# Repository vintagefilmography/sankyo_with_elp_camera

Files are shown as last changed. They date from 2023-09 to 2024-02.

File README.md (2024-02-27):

# sankyo_with_elp_camera  

elp_12mm_lens

This project is based on a Sankyo projector and ELP camera.  
Parts:  
Sankyo1000 projector  
The camera used is the usb ELP model ELP-USBFHD04H-FV. It uses an AR0330 sensor with 1080P resolution. 
Camera:  
https://www.amazon.com/gp/product/B01E8OX212/  
Light  
https://www.amazon.com/ULANZI-Waterproof-Lighting-Dimmable-Photography/dp/B098W63FJ5/  
Here is the result:  
[https://drive.google.com/file/d/1i-V...usp=share_link](https://drive.google.com/file/d/1_k86P1xBqTre0maZQDL-aEWelFFEkU7V/view?usp=sharing)  

This was scanned with the projector speed set to minimum which turns out to be around 7 frames per second.  

## Projector Mods
The 3 blade shutter wheel has to be removed. This is a bit involved project.
Refer to the following page for insstructions.  
https://github.com/vintagefilmography/Sankyo_shutter_wheel_removal  
https://github.com/vintagefilmography/Sankyo_gatemask_removal_v1  
Read both instructions and replace the gate mask once the shutter assembly is out.  
The heat shield and the fan shroud also have to be removed to provide enough space for the trigger components.  
Do not throw out any of the screws, you will need them later.
Replace the lamap with the LED light. You will have to 3D print the lamp bracket from the mechanical folder here.
It consists of two parts. Use 3mm screws. 
  

Print the camera adapter and attach it to the camera using 2mm screws and nuts.
Remove the old lens by pulling out on the focus knob (spring loaded) and by sliding the lensout. 
Slide the ecamera assembly into the lens holder. Make sure to pull out on the focus knob during the process.
If the camera fit is too tight then just send the adapter cylinder with sand paper.  
Make sure that the part is cleaned up properly after the process.

Install 150 Ohm 100W resistor in series with the rheostat slider to prevent the rheostat from overheating  
at low speeds.  
  

Print the trigger clip.
  
The trigger clip shaps onto the shutter wheel shaft as illustrated below.  
  
The trigger will have to be aligned properly once the trigger board is in place.
Order the trigger  board by contacting Stan Jelavic. You can send thee provate message in the forum.  
https://8mmforum.film-tech.com/vbb/forum/film-to-digital-conversion/86933-sankyo-projector-with-webcam-7fps-hd-resolution-synchronous-capture  
If you decide to make your own then send a message to Stan for the schematic info.
Connect the Arduino to the triggeer board.  
  
Slide the arduino from the front of the unit through the heatshield cutout towards the back of the unit.  


Align the trigger tab with the optocoupler bt sliding the trigger clip along the shaft.  
Additional trigger advance adjustment will be needed later.  
Mount the ardduino board in the top section of the unit just underneath the termnal strip.  
  
Make sure interconnect are dressed up nice and that theye are not interfering with any of the moving parts.  
Load thee film in.  
Advance the film manually by rotating the fan by pushing down on the fins.  
Adjust the trigger clip so that it is engaging the optocoupler roughly 10 degrees beefore the film starts moving down. 
This will have to be readjusted lated during capture so that it results in minimum flicker.  
Connect the arduino to the PC and program it with the arduino sw included here.  
Download cinecamV3 PC windows capture program from this site.  
Connect the arduino and the camera to the PC. Make sure that the trigger is not triggering the optocoupler  
since this could cause random mouse clicks.   
Run the cinecam program by executing the .exe file in the release directory.  

## Instructions for output video capture
Download cinecamv3.zip sw from here:  
https://drive.google.com/file/d/1sXQqYeeWrg85pbk6M5UWy_5RsJAFmLkf/view?usp=sharing   
Run the .exe file in release dir.  
The main window will open.   
Set camera selection to 0 or 1 depending on your system. Have to move the slider to the right until the numbers show up.  
Then back off the slider to get the right selection.  
Set fps to 18.
Set the output file destination.
Set width to 1500    Makae sure not to make mistakes here. Backspace dodes not work. Restart program if necessary.  
Set height to 1000 Same as above. Backspace edoes nott work.  
Press Start. The preview window will open up. Click Capture button. The output preview window will open up.
Leave the cursor on the capture button and run the projector on lowest speed.  
If running at lowest speed (may have to reset the rheostat stop screew for lowest speed) use an external fan   
and point it to the rheostat to prevent ot from overheating.  
Altenatively install a 150 Ohm 100W resistor in series with the rheostat slider terminal.  
That shouldd give you a nice low FPS range 5-10 FPS.  
Once done with the capture disconneect the arduino to prevent the mouse clicks. 
Click the Stop button. Make sure not to click on the Start button. That wowuld erase output file.
Once you click on the Stop button, rename the output file and  then you are done. 

## Instructions for output images capture
Download cinecamV3_images.zip sw from here:  
https://drive.google.com/drive/folders/1x1AzFv1zaV0cyByz2hpzGCwbrDphzmOL?usp=sharing   
Run the .exe file in release dir.  
The main window will open.   
Set camera selection to 0 or 1 depending on your system. Have to move the slider to the right until the numbers show up.  
Then back off the slider to get the right selection.  
Set fps to 18. Not used in image mode.
Set the output file destination. This entry contains the path to the images prefix. I.e. C:\capture\pics  
will generatate pict1,pict2,pict3,... image sequence. You can change this to suit your needs.  
Set width to 1500    Makae sure not to make mistakes here. Backspace dodes not work. Restart program if necessary.  
Set height to 1000 Same as above. Backspace edoes not work.  
Note that this setting works for the ELP cameras but may need to be changes for other camera types.  
Press Start. The preview window will open up. Click Capture button.  
Leave the cursor on the capture button and run the projector on lowest speed.  
Increase the projector speed until the app strats missing the fames.  
Then, back off a alittle bit.  
Once done with the capture disconneect the arduino to prevent the mouse clicks. 
Click the Stop button. Not reequired in this mode.

Postprocessing

Avisynth can be used for some postporcessig.  Get Avisynth from:
https://sourceforge.net/projects/avisynth2/
Here is the avisynth home page. You can skip it for now. It is just for your reference. http://avisynth.nl/index.php/Main_Page
Avisynth does not run as a standalone application. It is a tool that allows video editors and viewers to run the script.
The script is essentially a text file that contains avisynth commands for video processing.
One video tool that is very handy for video processing is called VirtualDub.
In addition to basic video processing, VirtialDub reads the avisynth script as well.
Download VirtualDub from here:
https://sourceforge.net/projects/vdfiltermod/files/  

Once done with the script, just drag the script file into the VirtualDub window.
After a minute or so the video first frame will be displayed.
In the video pulldown you can import filers for cropping, flipping horizontally etc.
At that point, set the video compression in the video pulldown and save the video.

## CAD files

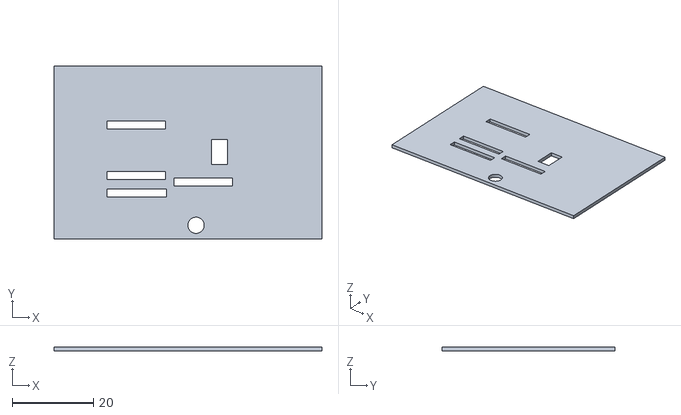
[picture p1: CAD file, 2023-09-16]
mechanical/optical_coupler_mockup1.stl
66.0 x 42.5 x 1.00

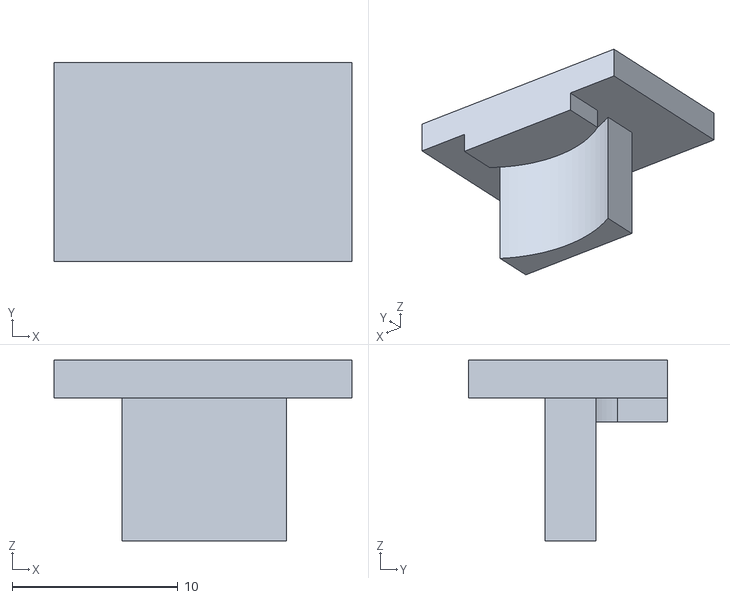
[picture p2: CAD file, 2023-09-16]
mechanical/lamp_clip.stl
18.0 x 12.0 x 10.9

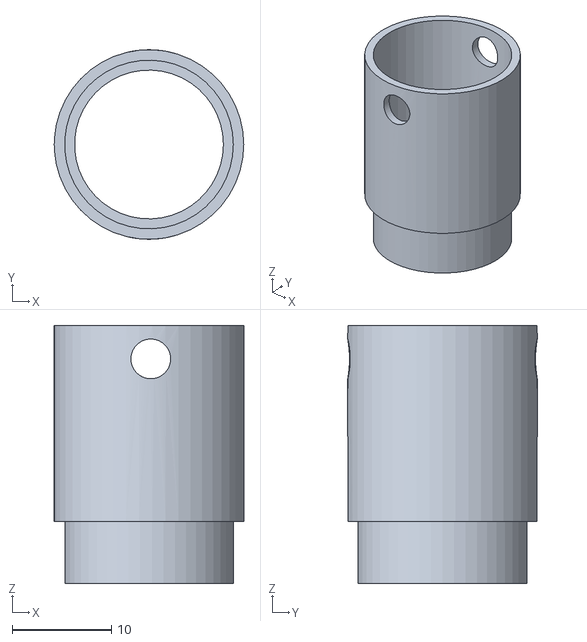
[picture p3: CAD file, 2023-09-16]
mechanical/lamp_post.stl
19.1 x 19.1 x 26.0

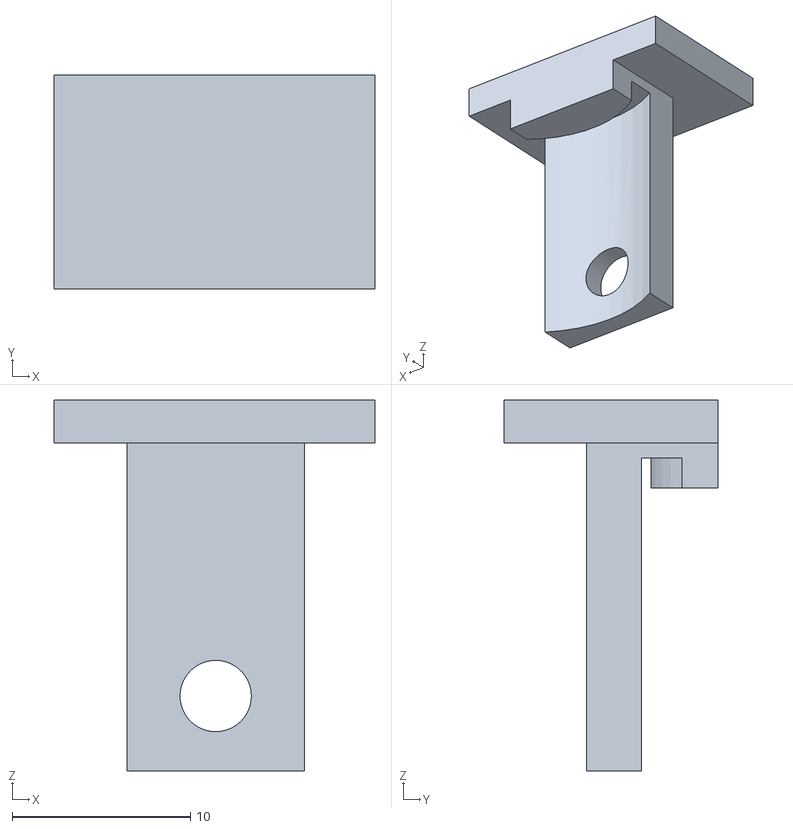
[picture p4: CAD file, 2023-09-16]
mechanical/lamp_mount_tab.stl
18.0 x 12.0 x 20.8

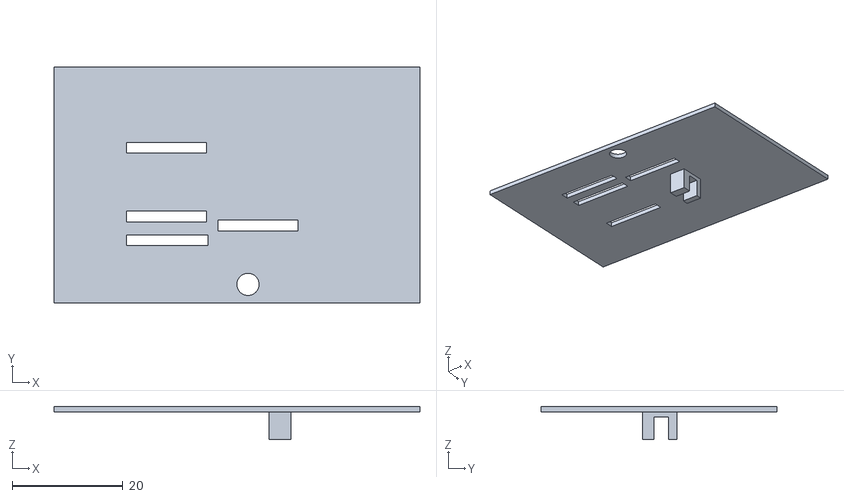
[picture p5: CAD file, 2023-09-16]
mechanical/optical_coupler_mockup.stl
66.0 x 42.5 x 6.00

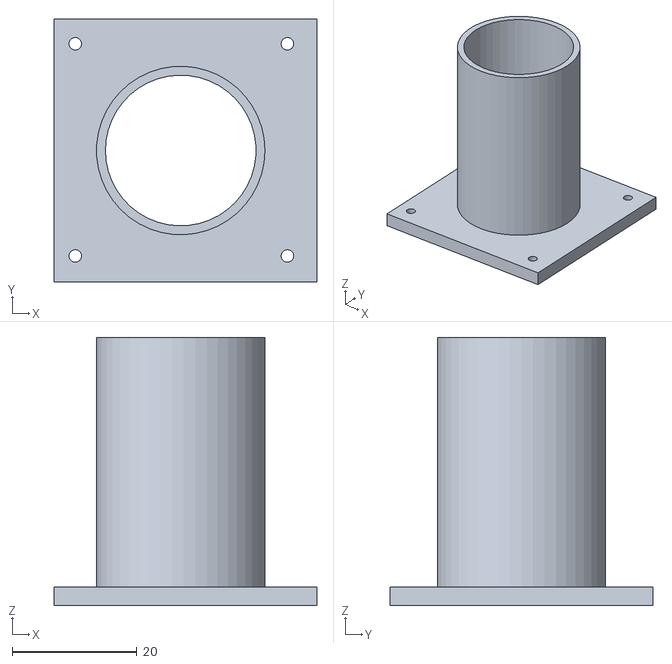
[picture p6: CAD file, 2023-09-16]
mechanical/camera_mount.stl
42.1 x 42.1 x 43.0

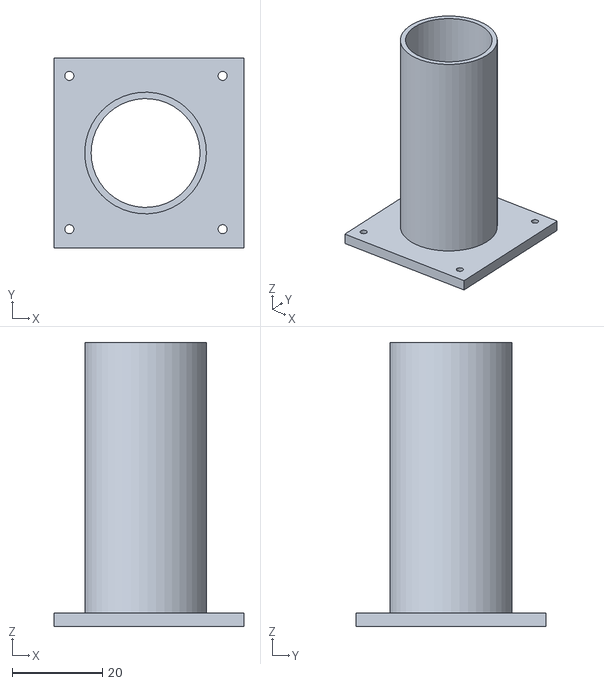
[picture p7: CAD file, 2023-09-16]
mechanical/camera_mount_16mm_lens.stl
42.1 x 42.1 x 63.0

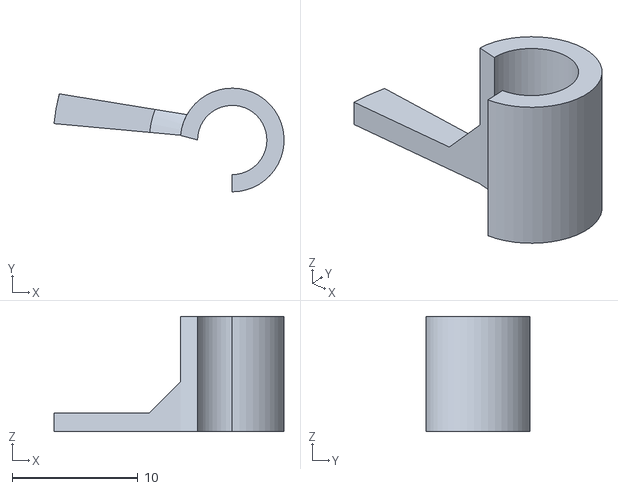
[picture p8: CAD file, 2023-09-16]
mechanical/trigger.stl
18.3 x 8.24 x 9.16

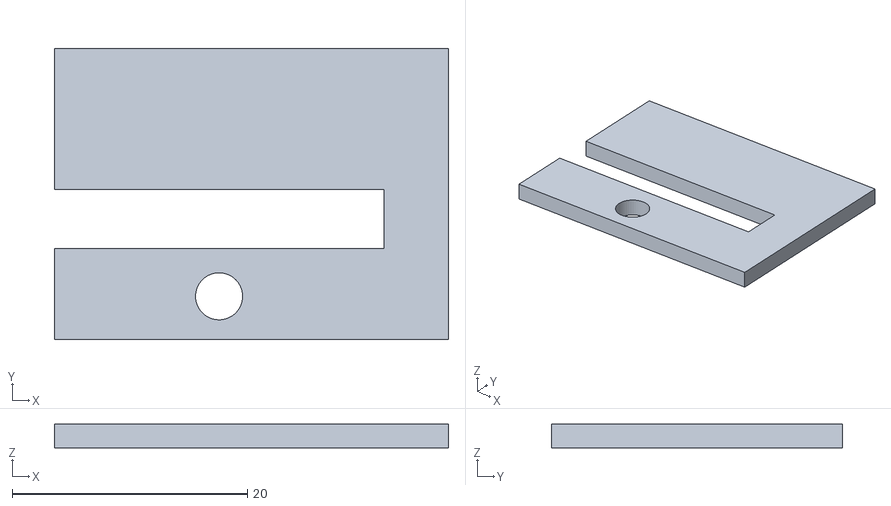
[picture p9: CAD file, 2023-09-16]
mechanical/arduino_bracket.stl
33.5 x 24.7 x 2.00

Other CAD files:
mechanical/lamp_post1.stl

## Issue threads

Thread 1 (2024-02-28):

Could not load file or assembly 'Emgu.CV.World'

sgraber, 2024-02-28:
I downloaded both cinecamV3 and cinecamV3_images and attempted to work with it.  I can use the slider to select the camera number and the frames per second; however, whenever I try to enter a number in the Width or Height boxes, the following error pops up.  This error presents itself with both of the above software executables.

Here is the Exception Text from the error:

************** Exception Text **************
System.IO.FileNotFoundException: Could not load file or assembly 'Emgu.CV.World, Version=3.1.0.2504, Culture=neutral, PublicKeyToken=7281126722ab4438' or one of its dependencies. The system cannot find the file specified.
File name: 'Emgu.CV.World, Version=3.1.0.2504, Culture=neutral, PublicKeyToken=7281126722ab4438'
   at emgu_test_app.Form1.OnKeyPress(KeyPressEventArgs ex)
   at System.Windows.Forms.Control.ProcessKeyEventArgs(Message& m)
   at System.Windows.Forms.Form.ProcessKeyPreview(Message& m)
   at System.Windows.Forms.Control.ProcessKeyMessage(Message& m)
   at System.Windows.Forms.Control.WmKeyChar(Message& m)
   at System.Windows.Forms.Control.WndProc(Message& m)
   at System.Windows.Forms.TextBoxBase.WndProc(Message& m)
   at System.Windows.Forms.TextBox.WndProc(Message& m)
   at System.Windows.Forms.NativeWindow.Callback(IntPtr hWnd, Int32 msg, IntPtr wparam, IntPtr lparam)

WRN: Assembly binding logging is turned OFF.
To enable assembly bind failure logging, set the registry value [HKLM\Software\Microsoft\Fusion!EnableLog] (DWORD) to 1.
Note: There is some performance penalty associated with assembly bind failure logging.
To turn this feature off, remove the registry value [HKLM\Software\Microsoft\Fusion!EnableLog].

************** Loaded Assemblies **************
mscorlib
    Assembly Version: 4.0.0.0
    Win32 Version: 4.8.9181.0 built by: NET481REL1LAST_C
    CodeBase: file:///C:/Windows/Microsoft.NET/Framework64/v4.0.30319/mscorlib.dll
----------------------------------------
emgu_test_app
    Assembly Version: 1.0.0.0
    Win32 Version: 1.0.0.0
    CodeBase: file:///C:/Users/sgrab/Downloads/cinecamV3/cinecamV3/emgu_test_app/obj/Release/emgu_test_app.exe
----------------------------------------
System.Windows.Forms
    Assembly Version: 4.0.0.0
    Win32 Version: 4.8.9181.0 built by: NET481REL1LAST_C
    CodeBase: file:///C:/WINDOWS/Microsoft.Net/assembly/GAC_MSIL/System.Windows.Forms/v4.0_4.0.0.0__b77a5c561934e089/System.Windows.Forms.dll
----------------------------------------
System
    Assembly Version: 4.0.0.0
    Win32 Version: 4.8.9220.0 built by: NET481REL1LAST_C
    CodeBase: file:///C:/WINDOWS/Microsoft.Net/assembly/GAC_MSIL/System/v4.0_4.0.0.0__b77a5c561934e089/System.dll
----------------------------------------
System.Drawing
    Assembly Version: 4.0.0.0
    Win32 Version: 4.8.9037.0 built by: NET481REL1
    CodeBase: file:///C:/WINDOWS/Microsoft.Net/assembly/GAC_MSIL/System.Drawing/v4.0_4.0.0.0__b03f5f7f11d50a3a/System.Drawing.dll
----------------------------------------
System.Configuration
    Assembly Version: 4.0.0.0
    Win32 Version: 4.8.9037.0 built by: NET481REL1
    CodeBase: file:///C:/WINDOWS/Microsoft.Net/assembly/GAC_MSIL/System.Configuration/v4.0_4.0.0.0__b03f5f7f11d50a3a/System.Configuration.dll
----------------------------------------
System.Core
    Assembly Version: 4.0.0.0
    Win32 Version: 4.8.9220.0 built by: NET481REL1LAST_C
    CodeBase: file:///C:/WINDOWS/Microsoft.Net/assembly/GAC_MSIL/System.Core/v4.0_4.0.0.0__b77a5c561934e089/System.Core.dll
----------------------------------------
System.Xml
    Assembly Version: 4.0.0.0
    Win32 Version: 4.8.9037.0 built by: NET481REL1
    CodeBase: file:///C:/WINDOWS/Microsoft.Net/assembly/GAC_MSIL/System.Xml/v4.0_4.0.0.0__b77a5c561934e089/System.Xml.dll
----------------------------------------

************** JIT Debugging **************
To enable just-in-time (JIT) debugging, the .config file for this
application or computer (machine.config) must have the
jitDebugging value set in the system.windows.forms section.
The application must also be compiled with debugging
enabled.

For example:

<configuration>
    <system.windows.forms jitDebugging="true" />
</configuration>

When JIT debugging is enabled, any unhandled exception
will be sent to the JIT debugger registered on the computer
rather than be handled by this dialog box.

sgraber, 2024-02-28:
Update to this issue:

1. Prior to unzipping the file, you must right click on the .zip, select Properties, and then check the box that says "Unblock," and then click Apply
2. You must run the emgu_test_app.exe program as Administrator (normal user level does not work)

Once these two things are done, the program functions as intended.

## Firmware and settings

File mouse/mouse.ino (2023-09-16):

/*

  ButtonMouseControl
  For Leonardo and Due boards only.
  Controls the mouse from five pushbuttons on an Arduino Leonardo, Micro or Due.

  Hardware:
  - five pushbuttons attached to D2, D3, D4, D5, D6
  The mouse movement is always relative. This sketch reads four pushbuttons,
  and uses them to set the movement of the mouse.
  WARNING: When you use the Mouse.move() command, the Arduino takes over your
  mouse! Make sure you have control before you use the mouse commands.

  created 15 Mar 2012
  modified 27 Mar 2012
  by Tom Igoe

  This example code is in the public domain.
  https://www.arduino.cc/en/Tutorial/ButtonMouseControl

*/

#include "Mouse.h"

// set pin numbers for the buttons:
const int mouseButton = 10;

int range = 5;              // output range of X or Y movement; affects movement speed
int responseDelay = 100;     // response delay of the mouse, in ms

void setup() 
{
	pinMode(mouseButton, INPUT);
  	//initialize mouse control:
  	Mouse.begin();
}

void loop() 
{
	int clickState = digitalRead(mouseButton);
	// if the mouse button is pressed:

	if (clickState == HIGH) 
	{
		// if the mouse is not pressed, press it:
		if (!Mouse.isPressed(MOUSE_LEFT)) 
		{
      			Mouse.press(MOUSE_LEFT);
            delay(responseDelay);
            Mouse.release(MOUSE_LEFT);
    }
  }
}
